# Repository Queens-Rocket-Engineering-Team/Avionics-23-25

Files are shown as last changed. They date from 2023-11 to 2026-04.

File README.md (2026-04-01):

# Legacy Repo!!
All QRET avionics hardware and firmware has migrated to:
- https://github.com/Queens-Rocket-Engineering-Team/av-recovery
- https://github.com/Queens-Rocket-Engineering-Team/av-instrumentation
- https://github.com/Queens-Rocket-Engineering-Team/av-telemetry
- http://github.com/Queens-Rocket-Engineering-Team/av-prop
- https://github.com/Queens-Rocket-Engineering-Team/av-power
- https://github.com/Queens-Rocket-Engineering-Team/av-libraries

# QRET Avionics (2023-2026)

This repository is the working space for QRET's 2023-2026 Avionics systems. This includes both hardware design and firmware projects.

If you're contributing, **make sure you're working in a branch other than Main.**

## Branch Naming Conventions
If you create a new branch, make sure its name includes:
- The subject you're working on
- Hardware (HW) or Firmware (FW)

Examples: `Altimeter_HW`, `Sensors_FW`

Currently we're using KiCAD 8.0.6.

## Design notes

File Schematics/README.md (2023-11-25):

# Schematics

This directory contains all schematics involved in this iteration of the Avionics system.

## Backplane
- Single, large PCB
- Connects all stack "modules" (PCBs)
- Allows communication between modules
- Cleaner routing for power

## GPS Module
- Acquires GPS signal
- Logs GPS data locally

## Communications Module
- Tracks data from other modules using CANBUS
- Remotely transmits data to ground station

## Altimter Module
- Tracks altitude using pressure and accelerometer
- Deploys parachute charges
- Logs altitude, pressure, events, etc. locally

## Sensors Module
- Has various on-board sensors
- Logs data from above sensors locally

## Power Module
- Facilitates connections between backplane and external devices
	- Batteries
	- Screw switches

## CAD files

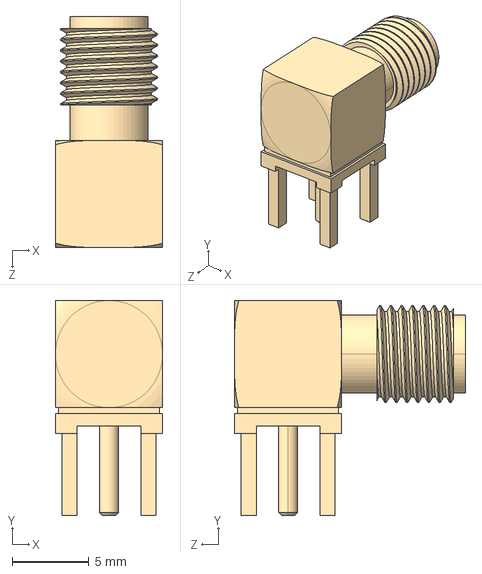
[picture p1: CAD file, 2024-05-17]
Schematics/Communications_Module/models/RF2-03E-T-00-50-G_SMA.STEP
7.00 x 14.1 x 15.1 mm

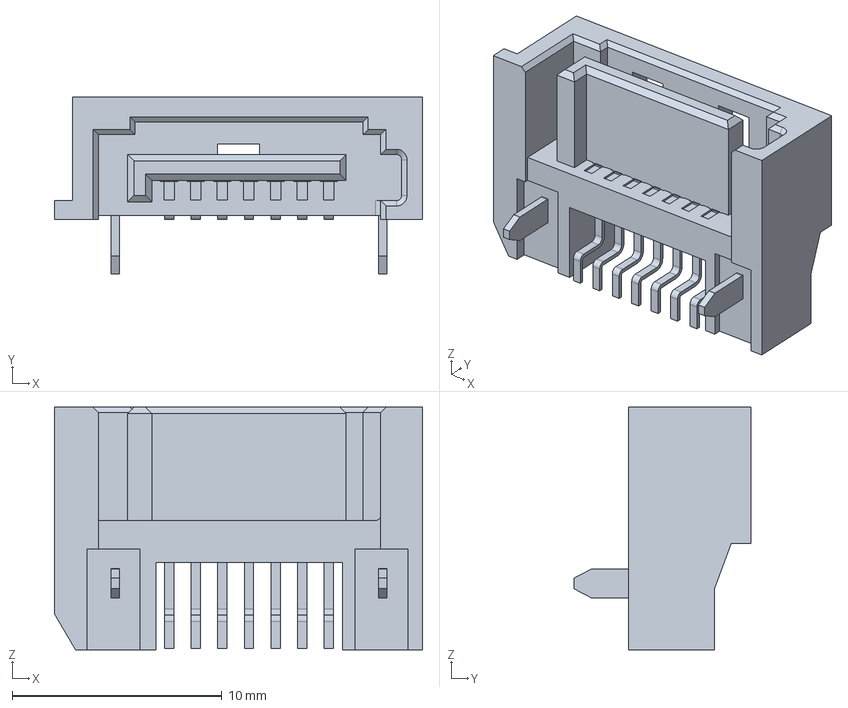
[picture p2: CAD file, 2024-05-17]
Schematics/GPS_Antenna_Board/models/CONN_47080-4001_MOL_SATA.stp
17.5 x 8.45 x 11.6 mm

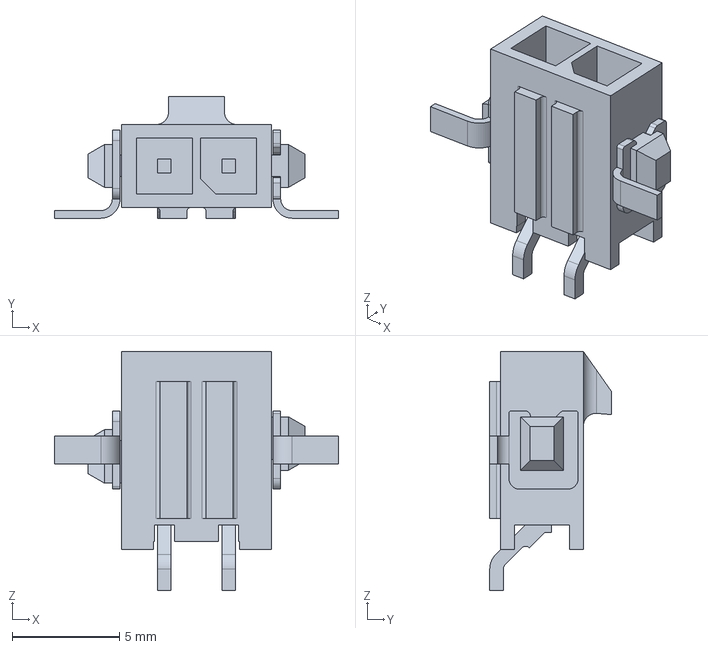
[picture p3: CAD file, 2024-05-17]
Schematics/Power_Module/models/c-2-1445057-2-d-3d.stp
13.2 x 5.67 x 11.2 mm

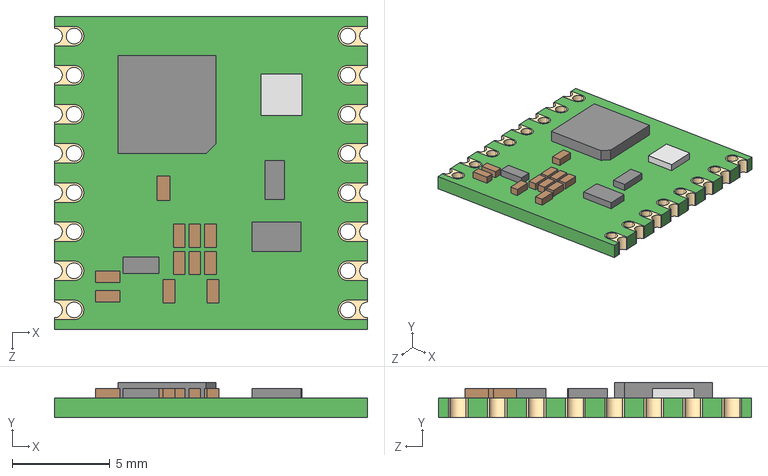
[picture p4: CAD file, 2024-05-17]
Schematics/Communications_Module/models/RFM95W-915S2.step
16.0 x 1.80 x 16.0 mm

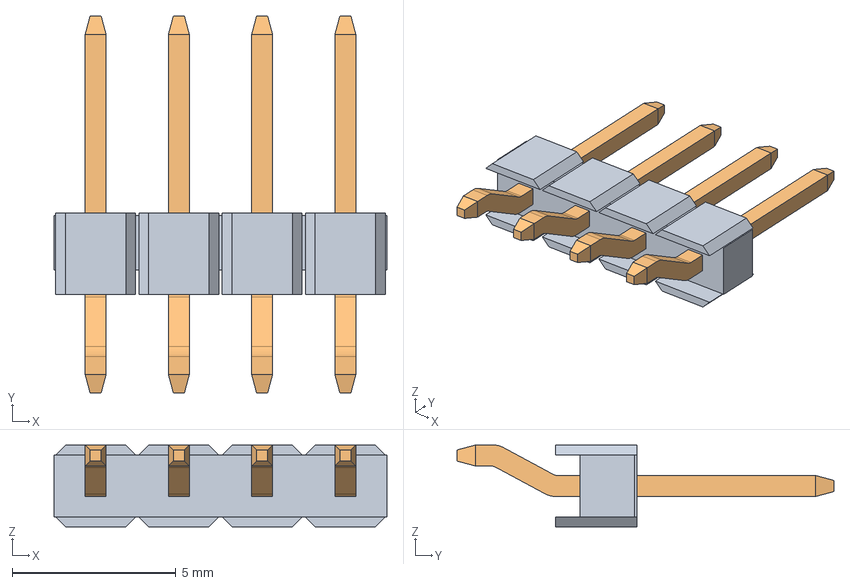
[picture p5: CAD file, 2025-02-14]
Schematics/Altimeter_Module/models/8890445_SWD_PINS.stp
10.2 x 11.5 x 2.50 mm

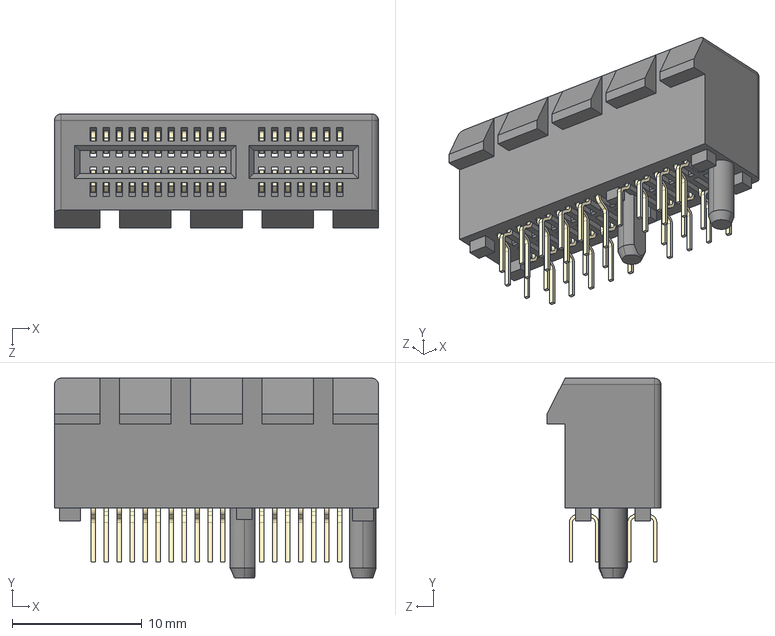
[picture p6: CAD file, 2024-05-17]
Schematics/Backplane/models/10018784-10210TLF.step
25.0 x 15.4 x 8.80 mm

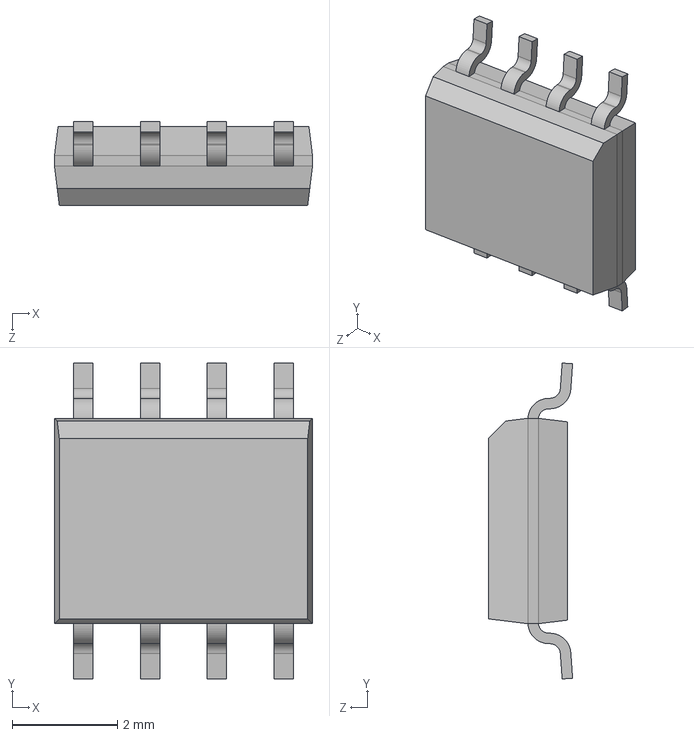
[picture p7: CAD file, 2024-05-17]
Schematics/Altimeter_Module/models/ACS70331EOLCTR-2P5U3.stp
4.90 x 6.00 x 1.60 mm

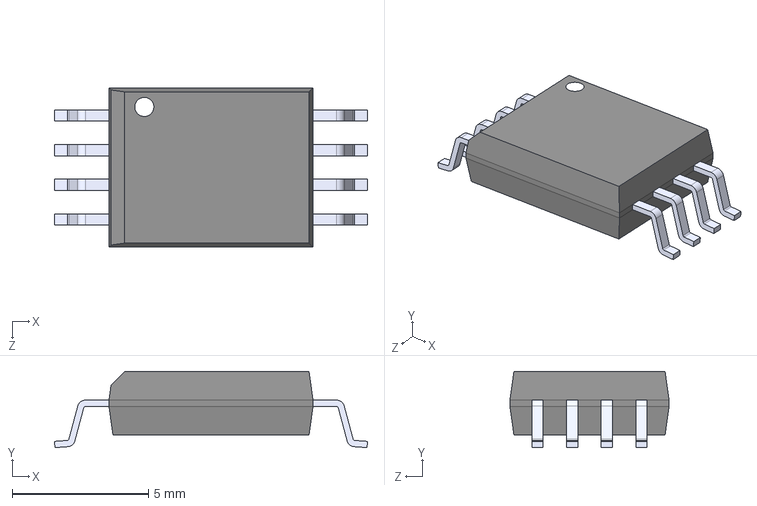
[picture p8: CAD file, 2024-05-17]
Schematics/GPS_Module/models/ISO1042BDWVR.step
11.5 x 2.80 x 5.85 mm

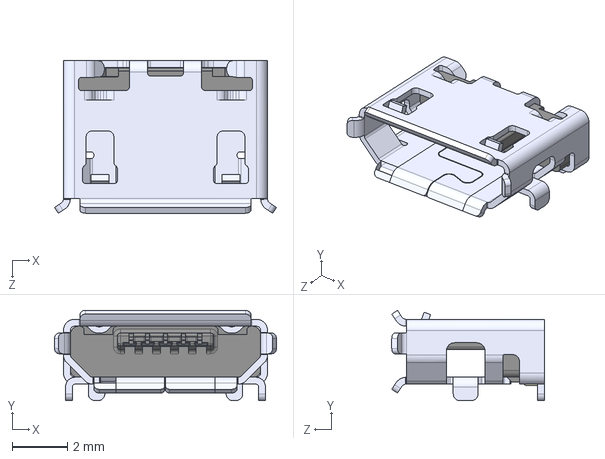
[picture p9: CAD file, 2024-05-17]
Schematics/GPS_Module/models/10118194-0001LF-USB.step
8.05 x 3.27 x 5.53 mm

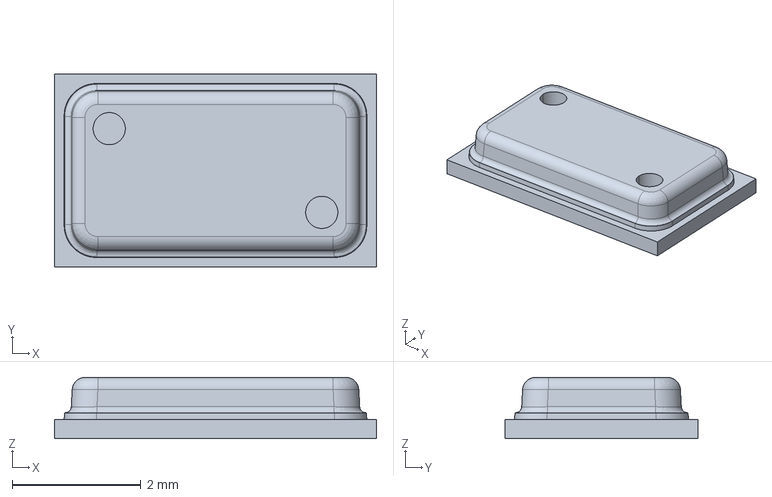
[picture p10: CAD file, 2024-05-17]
Schematics/Altimeter_Module/models/MS560702BA03-50.step
5.00 x 3.00 x 0.95 mm

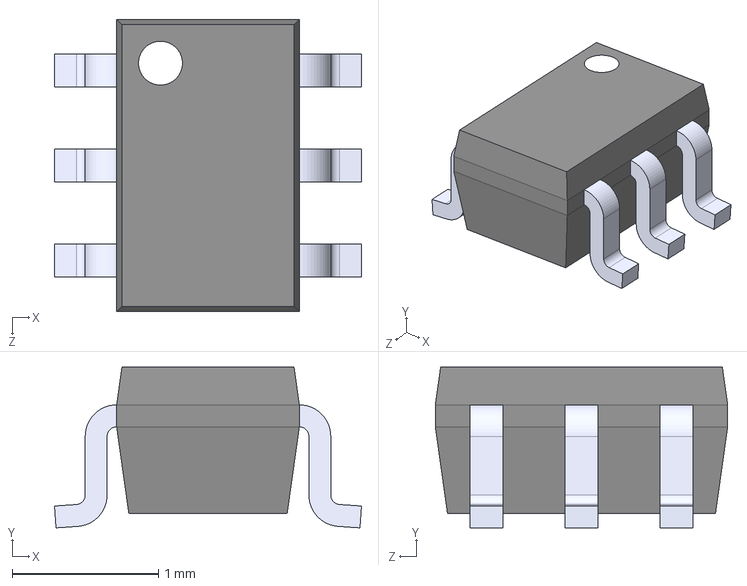
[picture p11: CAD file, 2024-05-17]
Schematics/GPS_Module/models/LM66100DCKR.step
2.10 x 1.10 x 2.00 mm

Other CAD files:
Schematics/Altimeter_Module/models/CONN_2-1445057-2_AMP.step

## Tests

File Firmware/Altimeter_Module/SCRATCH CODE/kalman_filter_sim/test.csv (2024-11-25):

Time | Actual Altitude | Measured Altitude | Estimated Altitude | Actual Velocity | Estimated Velocity
0 | 0.0045 | -0.1955 | -0.101693 | 0.3 | 0.195812
0.01 | 0.012 | 0.212 | 0.0209463 | 0.6 | 0.614993
0.02 | 0.0225 | -0.1775 | -0.0386365 | 0.9 | 0.84776
0.03 | 0.036 | 0.136 | 0.0205453 | 1.2 | 1.19597
0.04 | 0.0525 | 0.4525 | 0.153328 | 1.5 | 1.61529
0.05 | 0.072 | -0.228 | 0.0600471 | 1.8 | 1.80436
0.06 | 0.0945 | -0.4055 | -0.0534859 | 2.1 | 1.97128
0.07 | 0.12 | -0.08 | -0.0452763 | 2.4 | 2.25728
0.08 | 0.1485 | -0.3515 | -0.110828 | 2.7 | 2.46666
0.09 | 0.18 | -0.12 | -0.0942345 | 3 | 2.7561
0.1 | 0.2145 | -0.1855 | -0.0977243 | 3.3 | 3.02255
0.11 | 0.252 | 0.452 | 0.074034 | 3.6 | 3.46258
0.12 | 0.2925 | -0.00750001 | 0.0783585 | 3.9 | 3.72979
0.13 | 0.336 | 0.036 | 0.0952273 | 4.2 | 4.00786
0.14 | 0.3825 | 0.5825 | 0.257225 | 4.5 | 4.42828
0.15 | 0.432 | 0.832 | 0.445922 | 4.8 | 4.8702
0.16 | 0.4845 | 0.1845 | 0.411931 | 5.1 | 5.08501
0.17 | 0.54 | 0.94 | 0.592801 | 5.4 | 5.51353
0.18 | 0.5985 | 0.3985 | 0.58164 | 5.7 | 5.74474
0.19 | 0.66 | 0.26 | 0.537766 | 6 | 5.94092
0.2 | 0.7245 | 1.1245 | 0.74073 | 6.3 | 6.38298
0.21 | 0.792 | 0.392 | 0.694199 | 6.6 | 6.57112
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

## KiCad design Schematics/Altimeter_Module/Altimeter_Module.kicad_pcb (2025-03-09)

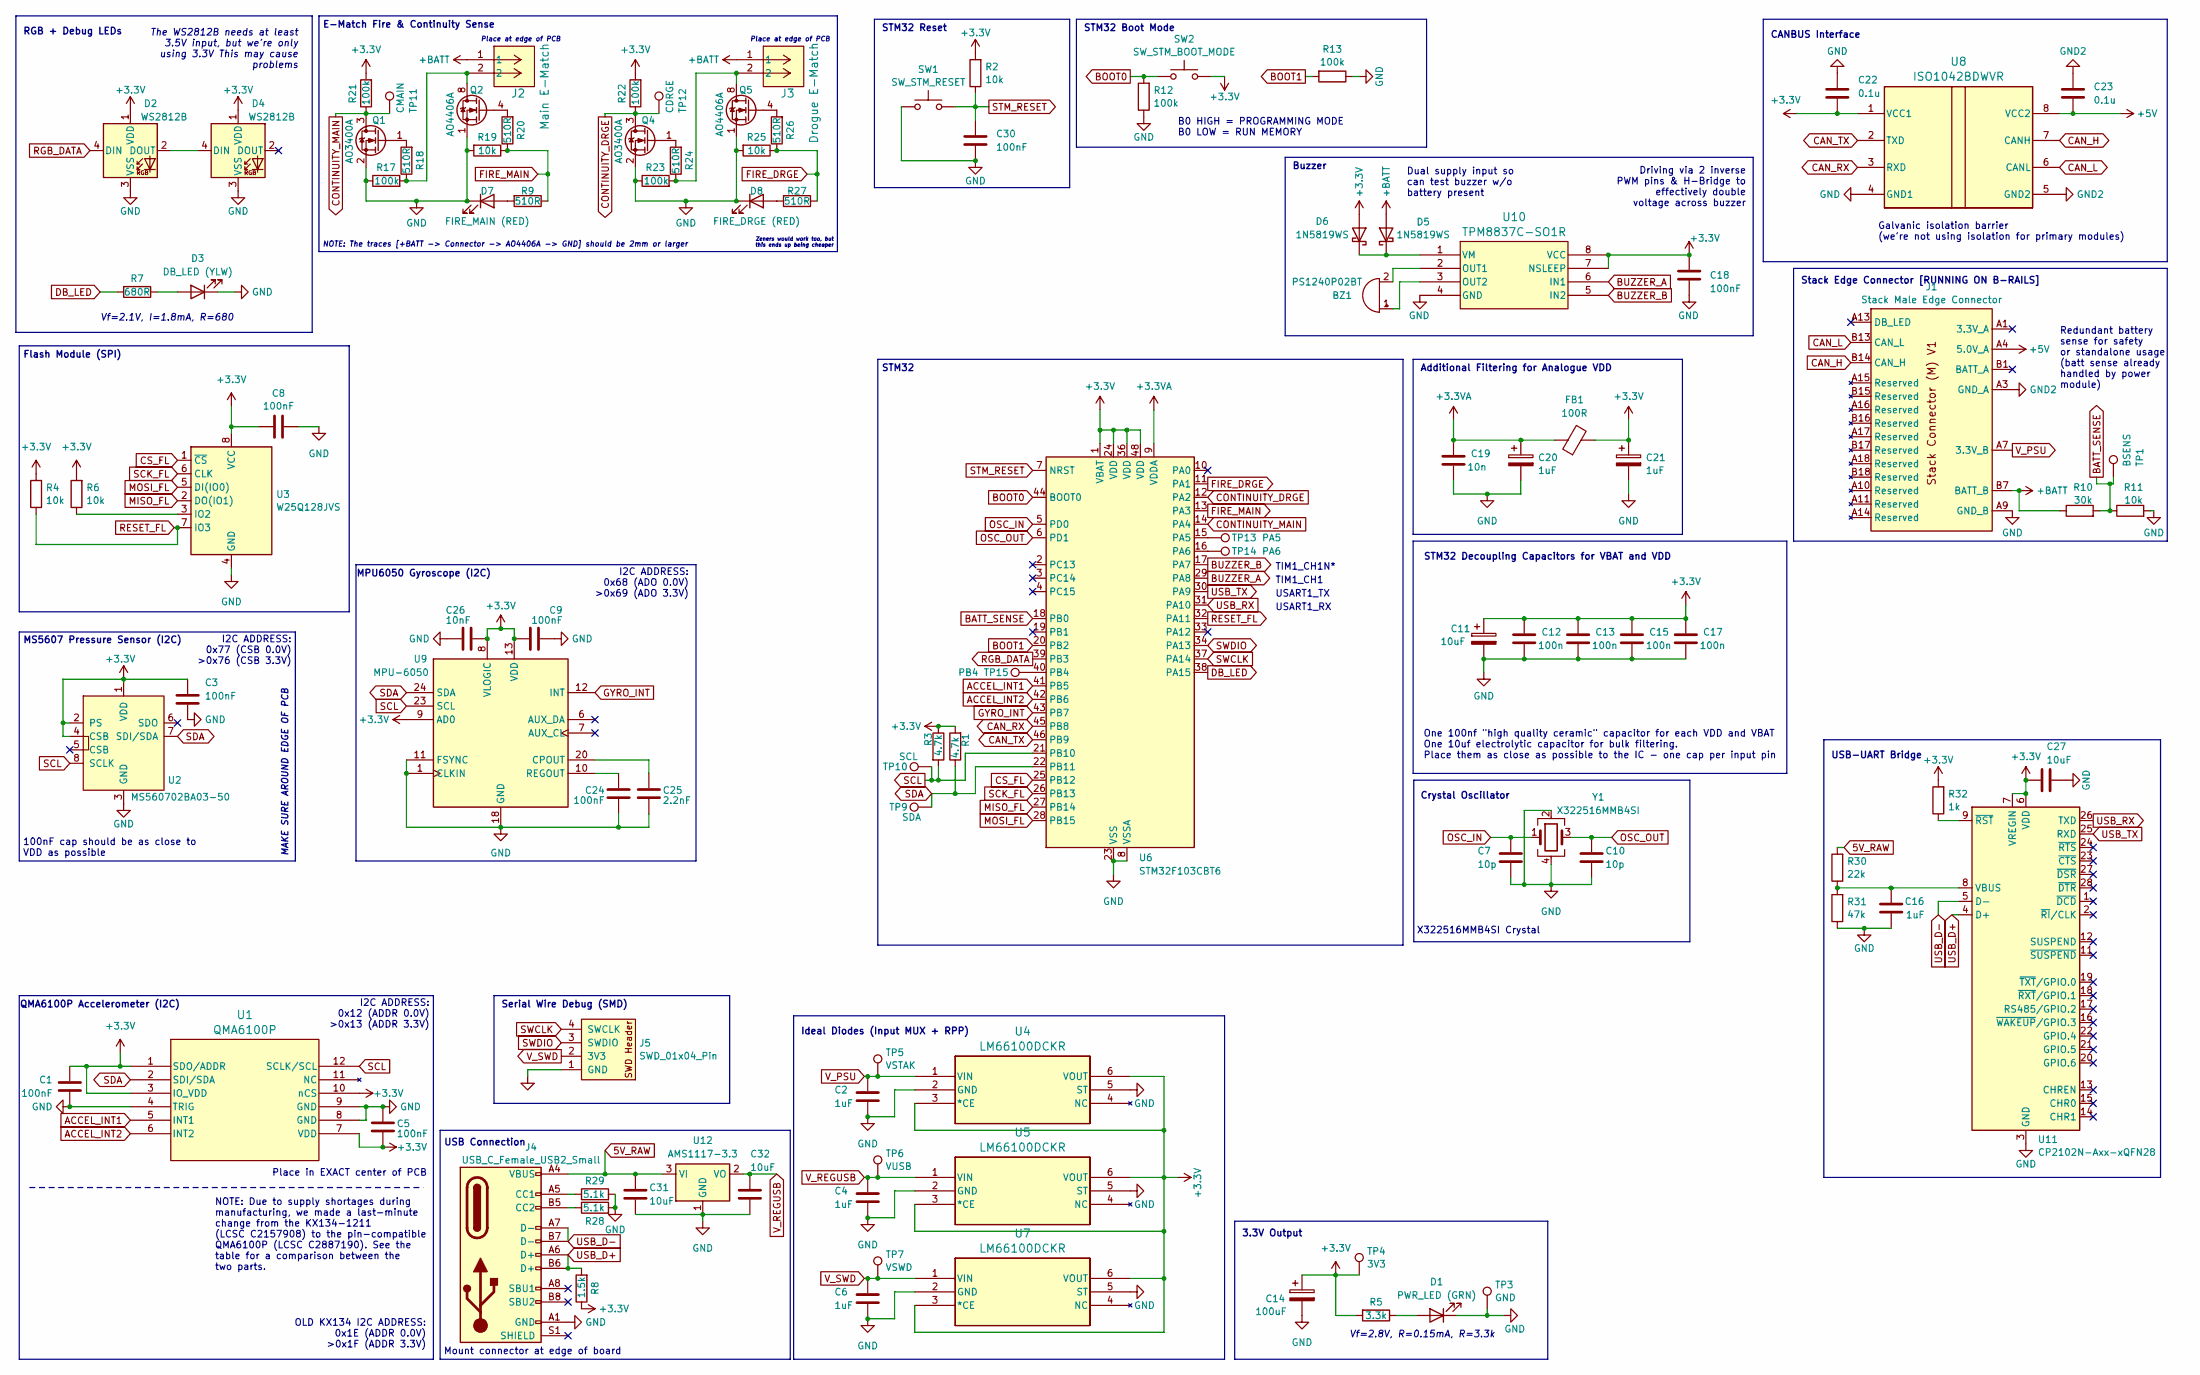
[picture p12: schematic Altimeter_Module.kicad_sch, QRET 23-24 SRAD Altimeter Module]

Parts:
BZ1: PS1240P02BT; Buzzer_12.6x9.5RM5.0; Digikey 445-2525-1-ND
C1, C3, C5, C8, C9, C18, C24, C30: 100nF; C_0603_1608Metric; JLCPCB C14663
C2, C4, C6, C16: 1uF; C_0603_1608Metric; JLCPCB C15849
C7, C10: 10p; C_0603_1608Metric; JLCPCB C1634
C11: 10uF; CP_Elec_4x5.4; Digikey 732-8411-1-ND
C12, C13, C15, C17: 100n; C_0402_1005Metric; JLCPCB C1525
C14: 100uF; CP_Elec_6.3x5.9; Digikey 732-8419-1-ND
C19: 10n; C_0603_1608Metric; JLCPCB C57112
C20, C21: 1uF; C_0805_2012Metric; JLCPCB C28323
C22, C23: 0.1u; C_0603_1608Metric; JLCPCB C14663
C25: 2.2nF; C_0603_1608Metric; JLCPCB C1604
C26: 10nF; C_0603_1608Metric; JLCPCB C57112
C27, C31, C32: 10uF; C_0603_1608Metric; JLCPCB C96446
D1: PWR_LED (GRN); LED_0805_2012Metric; JLCPCB C2297
D2, D4: WS2812B; LED_WS2812B_PLCC4_5.0x5.0mm_P3.2mm; Digikey 1568-COM-16347CT-ND
D3: DB_LED (YLW); LED_0603_1608Metric; JLCPCB C72038
D5, D6: 1N5819WS; D_SOD-323; JLCPCB C191023
D7: FIRE_MAIN (RED); LED_0603_1608Metric; JLCPCB C2286
D8: FIRE_DRGE (RED); LED_0603_1608Metric; JLCPCB C2286
FB1: 100R; R_0805_2012Metric; JLCPCB C1015
J1: Stack Male Edge Connector; BUS_PCIexpress_x1
J2: Main E-Match; CONN_2-1445057-2_TYCO; Digikey A33212CT-ND
J3: Drogue E-Match; CONN_2-1445057-2_TYCO; Digikey A33212CT-ND
J4: USB_C_Female_USB2_Small; USB_C_DB-108PWB; JLCPCB C5178541
J5: SWD_01x04_Pin; SWD_PinHeader_1x04_P2.54mm_Horizontal_SMD; Digikey 952-3233-ND
Q1, Q4: AO3400A; SOT-23; JLCPCB C20917
Q2, Q5: AO4406A; SOIC-8_3.9x4.9mm_P1.27mm; JLCPCB C5155213
R1, R3: 4.7k; R_0603_1608Metric; JLCPCB C23162
R2, R4, R6, R11, R19, R25: 10k; R_0603_1608Metric; JLCPCB C25804
R5: 3.3k; R_0603_1608Metric; JLCPCB C22978
R7: 680R; R_0603_1608Metric; JLCPCB C23228
R8: 1.5k; R_0603_1608Metric; JLCPCB C22843
R9, R18, R20, R24, R26, R27: 510R; R_0603_1608Metric; JLCPCB C23193
R10: 30k; R_0603_1608Metric; JLCPCB C22984
R12, R13, R17, R21, R22, R23: 100k; R_0603_1608Metric; JLCPCB C25803
R28, R29: 5.1k; R_0603_1608Metric; JLCPCB C23186
R30: 22k; R_0603_1608Metric; JLCPCB C31850
R31: 47k; R_0603_1608Metric; JLCPCB C25819
R32: 1k; R_0603_1608Metric; JLCPCB C21190
SW1: SW_STM_RESET; SW_Push_1P1T_XKB_TS-1187A; JLCPCB C318884
SW2: SW_STM_BOOT_MODE; SW_Push_1P1T_XKB_TS-1187A; JLCPCB C318884
TP1: BSENS; TestPoint_Pad_1.5x1.5mm
TP3: GND; TestPoint_Pad_1.5x1.5mm
TP4: 3V3; TestPoint_Pad_1.5x1.5mm
TP5: VSTAK; TestPoint_Pad_1.5x1.5mm
TP6: VUSB; TestPoint_Pad_1.5x1.5mm
TP7: VSWD; TestPoint_Pad_1.5x1.5mm
TP9: SDA; TestPoint_Pad_1.5x1.5mm
TP10: SCL; TestPoint_Pad_1.5x1.5mm
TP11: CMAIN; TestPoint_Pad_1.5x1.5mm
TP12: CDRGE; TestPoint_Pad_1.5x1.5mm
TP13: PA5; TestPoint_Pad_1.5x1.5mm
TP14: PA6; TestPoint_Pad_1.5x1.5mm
TP15: PB4; TestPoint_Pad_1.5x1.5mm
U1: QMA6100P; LGA-12_2x2mm_P0.5mm; JLCPCB C2887190
U2: MS560702BA03-50; MS5607_Handsolder; Digikey 223-1198-1-ND
U3: W25Q128JVS; SOIC-8_5.23x5.23mm_P1.27mm; JLCPCB C97521
U4, U5, U7: LM66100DCKR; SC-70-6_Handsoldering; JLCPCB C2869734
U6: STM32F103CBT6; LQFP-48_7x7mm_P0.5mm; JLCPCB C8304
U8: ISO1042BDWVR; SOIC-8 ISO1042BDWV; JLCPCB C484409
U9: MPU-6050; InvenSense_QFN-24_4x4mm_P0.5mm; JLCPCB C24112
U10: TPM8837C-SO1R; SOP-8_TPK; Digikey 5503-TPM8837C-SO1RCT-ND
U11: CP2102N-Axx-xQFN28; QFN-28-1EP_5x5mm_P0.5mm_EP3.35x3.35mm; JLCPCB C6568
U12: AMS1117-3.3; SOT-223-3_TabPin2; JLCPCB C6186
Y1: X322516MMB4SI; Crystal_SMD_3225-4Pin_3.2x2.5mm; JLCPCB C13738

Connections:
5V_RAW: C31.1, J4.A4 (VBUS), J4.A9 (VBUS), J4.B4 (VBUS), J4.B9 (VBUS), R30.2, U12.3 (VI)
+3.3V: C1.1, C3.1, C5.2, C8.1, C9.1, C11.1, C12.1, C13.1, C14.1, C15.1, C17.1, C18.1, C21.1, C22.2, C26.1, C27.2, D2.1 (VDD), D4.1 (VDD), D6.2 (A), FB1.2, R1.2, R2.2, R3.1, R4.2, R5.2, R6.2, R8.1, R21.2, R22.2, R32.2, SW2.2, TP4.1, U1.1 (SDO/ADDR), U1.3 (IO_VDD), U1.7 (VDD), U1.10 (nCS), U2.1 (VDD), U2.2 (PS), U2.4 (CSB), U3.8 (VCC), U4.3 (*CE), U4.6 (VOUT), U5.3 (*CE), U5.6 (VOUT), U6.1 (VBAT), U6.24 (VDD), U6.36 (VDD), U6.48 (VDD), U7.3 (*CE), U7.6 (VOUT), U8.1 (VCC1), U9.8 (VLOGIC), U9.9 (AD0), U9.13 (VDD), U10.7 (NSLEEP), U10.8 (VCC), U11.6 (VDD), U11.7 (VREGIN)
+3.3VA: C19.1, C20.1, FB1.1, U6.9 (VDDA)
+5V: C23.2, J1.A4 (5.0V_A), J1.A5 (5.0V_A), U8.8 (VCC2)
+BATT: D5.2 (A), J1.B7 (BATT_B), J1.B8 (BATT_B), J1.B9 (BATT_B), J2.1, J3.1, R10.1
ACCEL_INT1: U1.5 (INT1), U6.41 (PB5)
ACCEL_INT2: U1.6 (INT2), U6.42 (PB6)
BATT_SENSE: R10.2, R11.1, TP1.1, U6.18 (PB0)
BOOT0: R12.2, SW2.1, U6.44 (BOOT0)
BOOT1: R13.2, U6.20 (PB2)
BUZZER_A: U6.29 (PA8), U10.6 (IN1)
BUZZER_B: U6.17 (PA7), U10.5 (IN2)
CAN_H: J1.B14 (CAN_H), U8.7 (CANH)
CAN_L: J1.B13 (CAN_L), U8.6 (CANL)
CAN_RX: U6.45 (PB8), U8.3 (RXD)
CAN_TX: U6.46 (PB9), U8.2 (TXD)
CONTINUITY_DRGE: Q4.3 (D), R22.1, TP12.1, U6.12 (PA2)
CONTINUITY_MAIN: Q1.3 (D), R21.1, TP11.1, U6.14 (PA4)
CS_FL: U3.1 (~CS), U6.25 (PB12)
DB_LED: R7.2, U6.38 (PA15)
FIRE_DRGE: R25.1, R26.1, R27.1, U6.11 (PA1)
FIRE_MAIN: R9.1, R19.1, R20.1, U6.13 (PA3)
GND: C1.2, C2.2, C3.2, C4.2, C5.1, C6.2, C7.2, C8.2, C9.2, C10.2, C11.2, C12.2, C13.2, C14.2, C15.2, C16.1, C17.2, C18.2, C19.2, C20.2, C21.2, C22.1, C24.2, C25.2, C26.2, C27.1, C30.2, C31.2, C32.2, D1.1 (K), D2.3 (VSS), D3.1 (K), D4.3 (VSS), D7.1 (K), D8.1 (K), J1.A9 (GND_B), J1.A12 (GND_B), J1.B10 (GND_B), J1.B11 (GND_B), J1.B12 (GND_B), J4.A1 (GND), J4.A12 (GND), J4.B1 (GND), J4.B12 (GND), J5.1 (GND), Q1.2 (S), Q2.1 (S), Q2.2 (S), Q2.3 (S), Q4.2 (S), Q5.1 (S), Q5.2 (S), Q5.3 (S), R11.2, R12.1, R13.1, R17.1, R19.2, R23.1, R25.2, R28.2, R29.2, R31.1, SW1.1, TP3.1, U1.4 (TRIG), U1.8 (GND), U1.9 (GND), U2.3 (GND), U3.4 (GND), U4.2 (GND), U4.5 (ST), U5.2 (GND), U5.5 (ST), U6.8 (VSSA), U6.23 (VSS), U6.35 (VSS), U6.47 (VSS), U7.2 (GND), U7.5 (ST), U8.4 (GND1), U9.1 (CLKIN), U9.11 (FSYNC), U9.18 (GND), U10.4 (GND), U11.3 (GND), U11.29 (GND), U12.1 (GND), Y1.2, Y1.4
GND2: C23.1, J1.A3 (GND_A), J1.A6 (GND_A), J1.B4 (GND_A), J1.B5 (GND_A), J1.B6 (GND_A), U8.5 (GND2)
GYRO_INT: U6.43 (PB7), U9.12 (INT)
MISO_FL: U3.2 (DO(IO1)), U6.27 (PB14)
MOSI_FL: U3.5 (DI(IO0)), U6.28 (PB15)
unnamed: BZ1.2 (+), U10.2 (OUT1)
unnamed: BZ1.1 (-), U10.3 (OUT2)
unnamed: D1.2 (A), R5.1
unnamed: D2.2 (DOUT), D4.4 (DIN)
unnamed: D3.2 (A), R7.1
unnamed: D5.1 (K), D6.1 (K), U10.1 (VM)
unnamed: D7.2 (A), R9.2
unnamed: D8.2 (A), R27.2
unnamed: J2.2, Q2.5 (D), Q2.6 (D), Q2.7 (D), Q2.8 (D), R17.2, R18.1
unnamed: J3.2, Q5.5 (D), Q5.6 (D), Q5.7 (D), Q5.8 (D), R23.2, R24.1
unnamed: J4.A5 (CC1), R29.1
unnamed: J4.B5 (CC2), R28.1
unnamed: Q1.1 (G), R18.2
unnamed: Q2.4 (G), R20.2
unnamed: Q4.1 (G), R24.2
unnamed: Q5.4 (G), R26.2
unnamed: R6.1, U3.3 (IO2)
unnamed: TP13.1, U6.15 (PA5)
unnamed: TP14.1, U6.16 (PA6)
unnamed: TP15.1, U6.40 (PB4)
unnamed: C25.1, U9.20 (CPOUT)
unnamed: C24.1, U9.10 (REGOUT)
unnamed: C16.2, R30.1, R31.2, U11.8 (VBUS)
unnamed: R32.1, U11.9 (~RST)
OSC_IN: C7.1, U6.5 (PD0), Y1.1
OSC_OUT: C10.1, U6.6 (PD1), Y1.3
RESET_FL: R4.1, U3.7 (IO3), U6.32 (PA11)
RGB_DATA: D2.4 (DIN), U6.39 (PB3)
SCK_FL: U3.6 (CLK), U6.26 (PB13)
SCL: R3.2, TP10.1, U1.12 (SCLK/SCL), U2.8 (SCLK), U6.21 (PB10), U9.23 (SCL)
SDA: R1.1, TP9.1, U1.2 (SDI/SDA), U2.7 (SDI/SDA), U6.22 (PB11), U9.24 (SDA)
STM_RESET: C30.1, R2.1, SW1.2, U6.7 (NRST)
SWCLK: J5.4 (SWCLK), U6.37 (PA14)
SWDIO: J5.3 (SWDIO), U6.34 (PA13)
USB_D+: J4.A6 (D+), J4.B6 (D+), R8.2, U11.4 (D+)
USB_D-: J4.A7 (D-), J4.B7 (D-), U11.5 (D-)
USB_RX: U6.31 (PA10), U11.26 (TXD)
USB_TX: U6.30 (PA9), U11.25 (RXD)
V_PSU: C2.1, J1.A7 (3.3V_B), J1.A8 (3.3V_B), TP5.1, U4.1 (VIN)
V_REGUSB: C4.1, C32.1, TP6.1, U5.1 (VIN), U12.2 (VO)
V_SWD: C6.1, J5.2 (3V3), TP7.1, U7.1 (VIN)

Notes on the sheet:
Serial Wire Debug (SMD)
Flash Module (SPI)
RGB + Debug LEDs
The WS2812B needs at least 3.5V input, but we're only using 3.3V This may cause problems
Additional Filtering for Analogue VDD
Stack Edge Connector [RUNNING ON B-RAILS]
NOTE: Due to supply shortages during manufacturing, we made a last-minute change from the KX134-1211 (LCSC C2157908) to the pin-compatible QMA6100P (LCSC C2887190). See the table for a comparison between the two parts.
Buzzer
Place at edge of PCB
Ideal Diodes (Input MUX + RPP)
Crystal Oscillator
Vf=2.1V, I=1.8mA, R=680
STM32
I2C ADDRESS: 0x12 (ADDR 0.0V) >0x13 (ADDR 3.3V)
B0 HIGH = PROGRAMMING MODE B0 LOW = RUN MEMORY
USART1_TX
USART1_RX
MS5607 Pressure Sensor (I2C)
Place in EXACT center of PCB
3.3V Output
OLD KX134 I2C ADDRESS: 0x1E (ADDR 0.0V) >0x1F (ADDR 3.3V)
Mount connector at edge of board
X322516MMB4SI Crystal
CANBUS Interface
STM32 Decoupling Capacitors for VBAT and VDD
I2C ADDRESS: 0x68 (ADO 0.0V) >0x69 (ADO 3.3V)
STM32 Boot Mode
TIM1_CH1N*
TIM1_CH1
QMA6100P Accelerometer (I2C)
E-Match Fire & Continuity Sense
Galvanic isolation barrier (we're not using isolation for primary modules)
One 100nf "high quality ceramic" capacitor for each VDD and VBAT One 10uf electrolytic capacitor for bulk filtering. Place them as close as possible to the IC - one cap per input pin
NOTE: The traces [+BATT -> Connector -> AO4406A -> GND] should be 2mm or larger
Zeners would work too, but this ends up being cheaper
MAKE SURE AROUND EDGE OF PCB
Driving via 2 inverse PWM pins & H-Bridge to effectively double voltage across buzzer
100nF cap should be as close to VDD as possible
I2C ADDRESS: 0x77 (CSB 0.0V) >0x76 (CSB 3.3V)
STM32 Reset

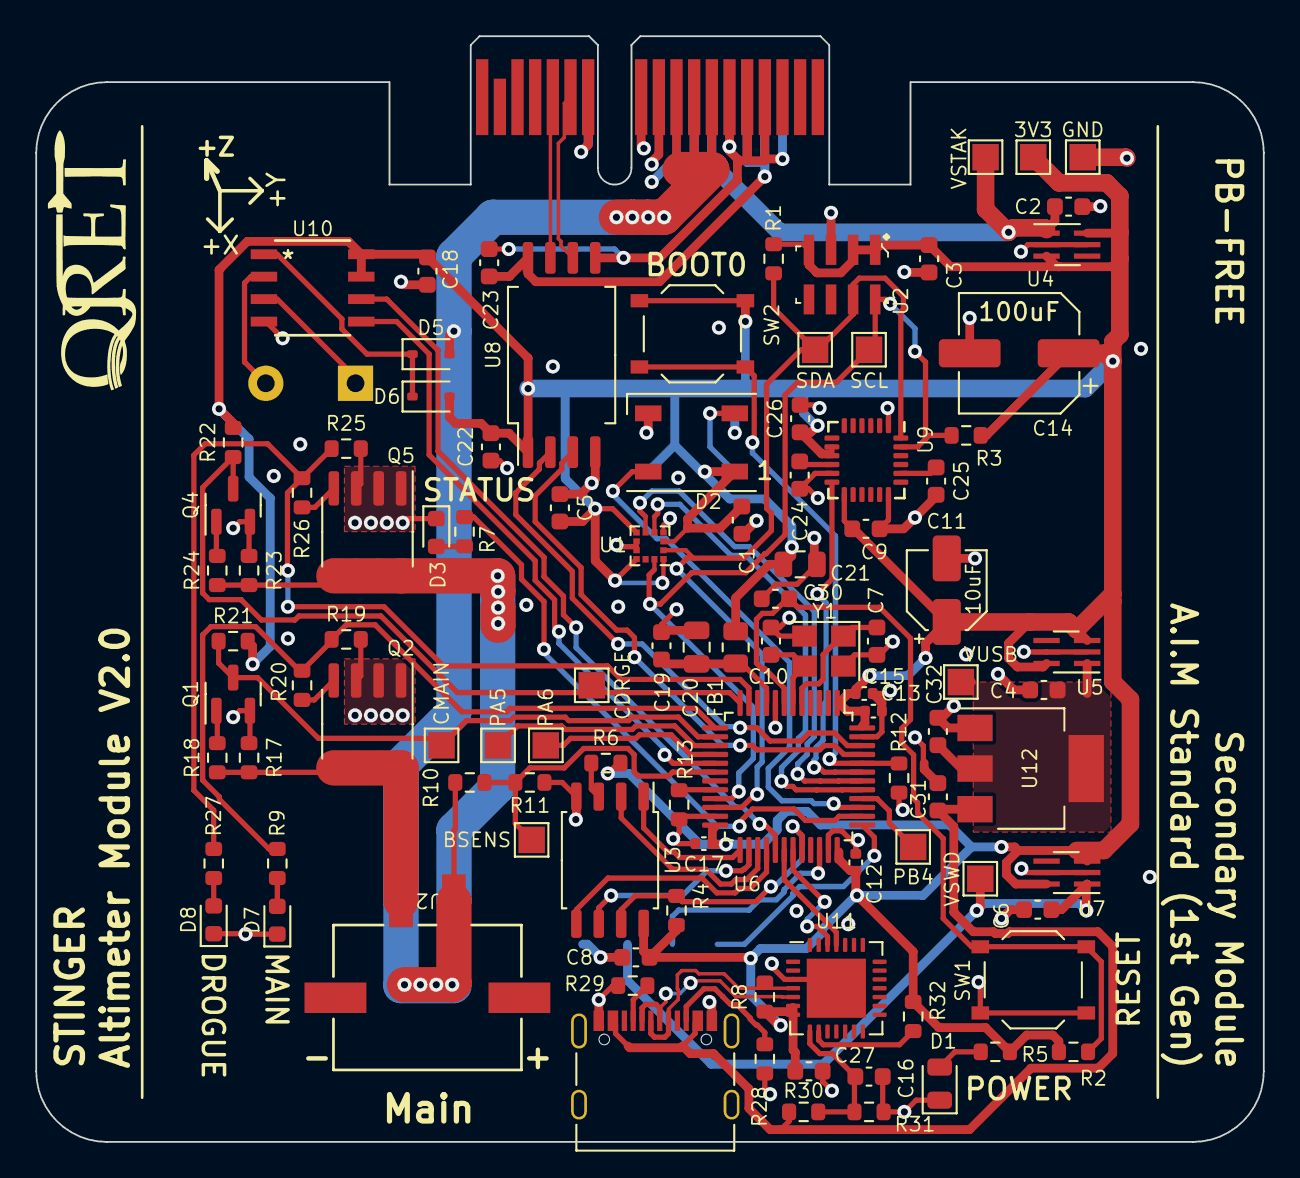
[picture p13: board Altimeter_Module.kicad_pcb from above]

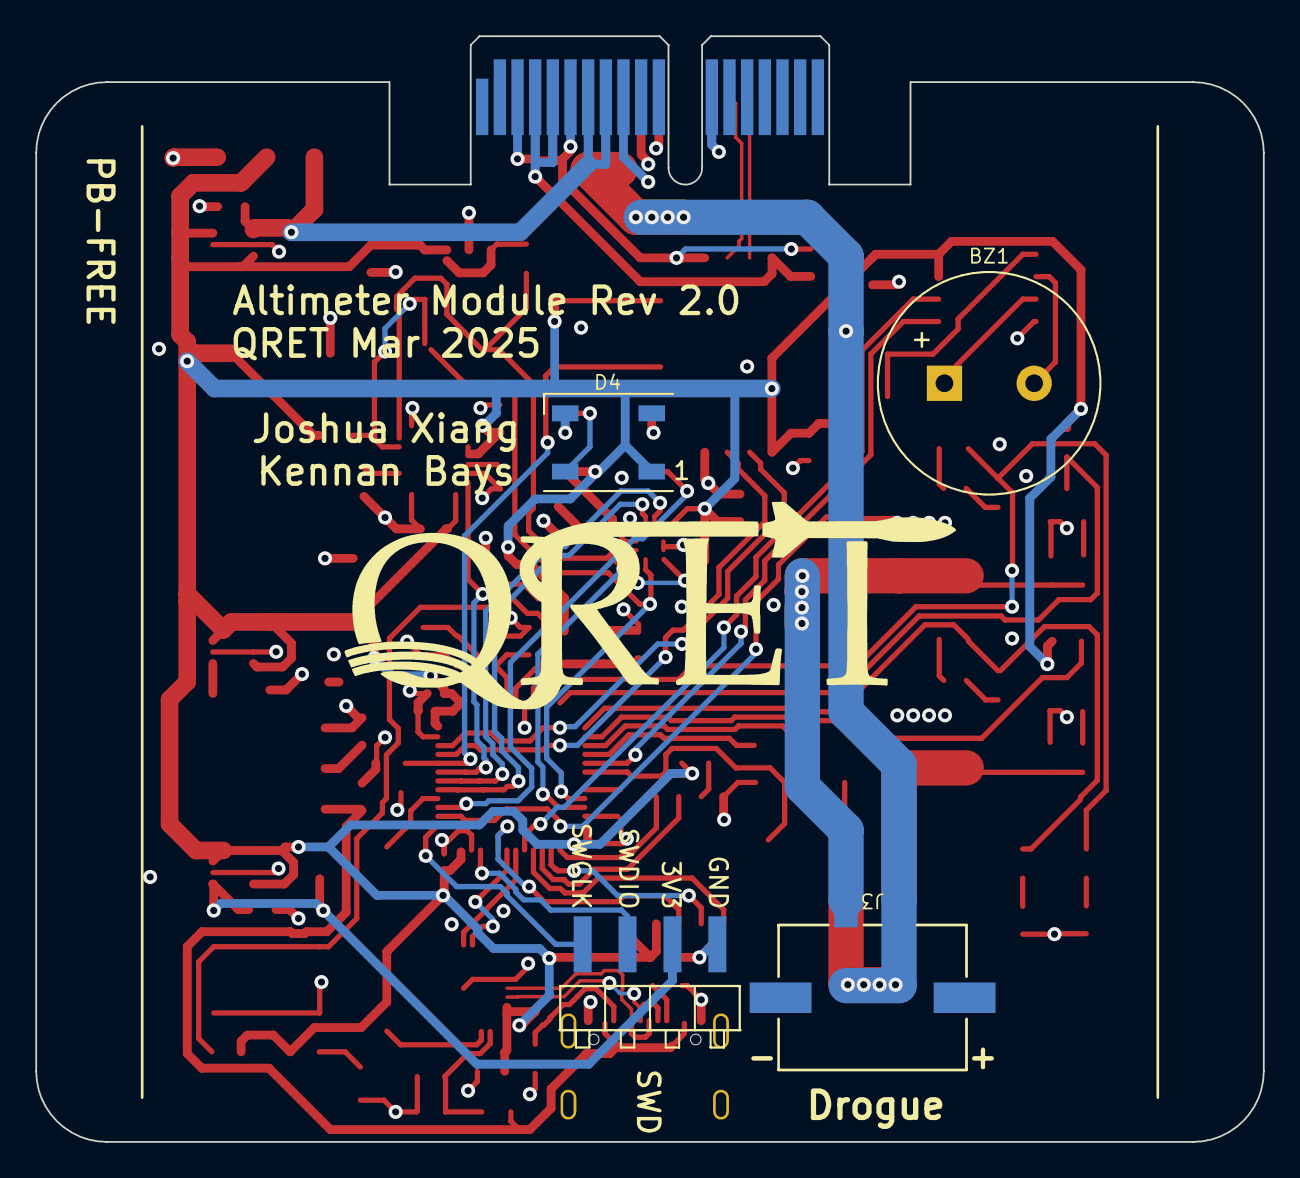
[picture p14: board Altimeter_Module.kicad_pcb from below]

Board: 4 copper layers, 69.5 x 62.6 mm, 106 parts (4 on the bottom side), 68 nets.

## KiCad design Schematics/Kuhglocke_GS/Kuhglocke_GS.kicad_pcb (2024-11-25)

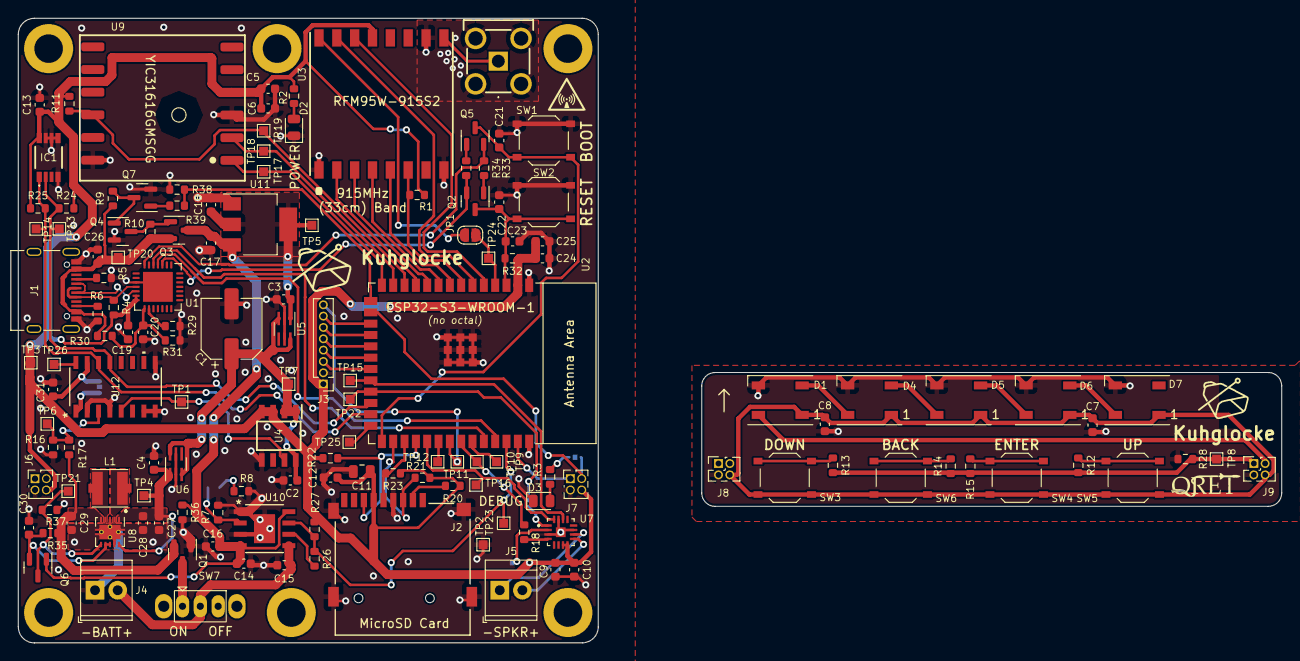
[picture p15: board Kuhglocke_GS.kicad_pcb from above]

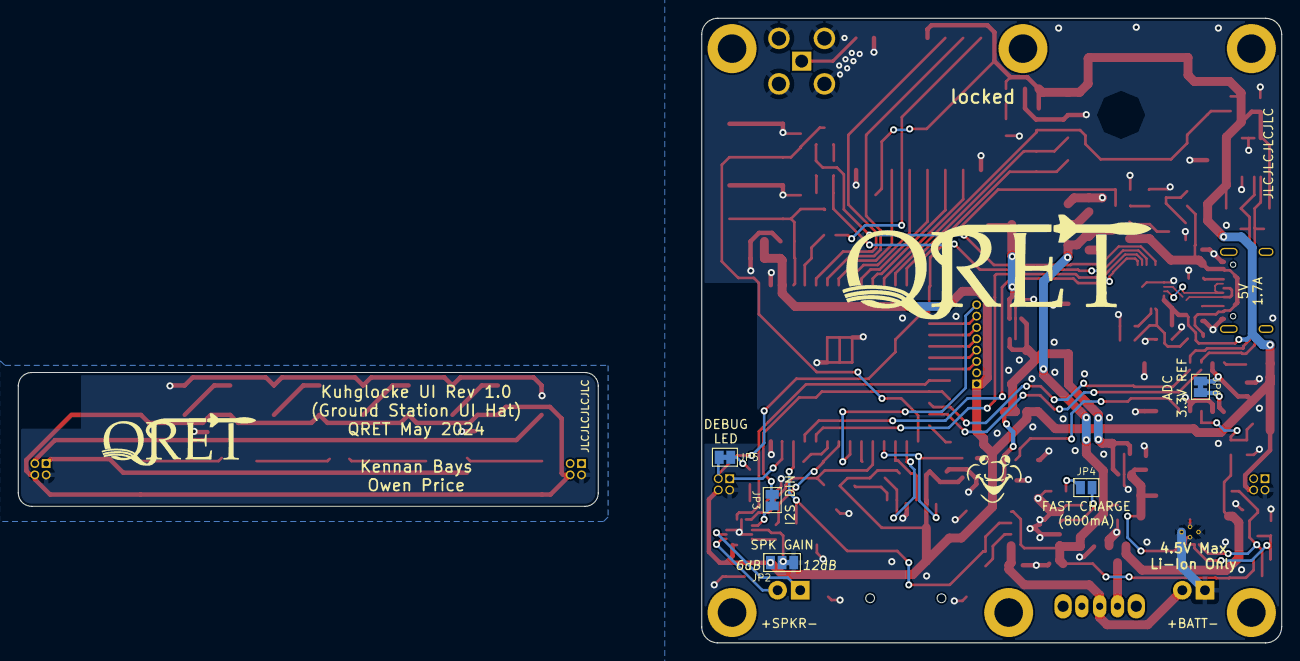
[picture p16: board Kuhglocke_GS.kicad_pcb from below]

Board: 2 copper layers, 65.0 x 70.0 mm, 152 parts (5 on the bottom side), 94 nets.

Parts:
AE1: Antenna; PCB114SMAFRAJA
C1: 100uF; CP_Elec_6.3x5.9
C2, C5, C9, C12, C13, C16, C21, C22, C25, C30: 0.1uF; C_0603_1608Metric
C3, C4, C7, C8, C14, C15, C20, C23, C31: 1uF; C_0603_1608Metric
C6: 4.7uF; C_0603_1608Metric
C10, C17, C18, C19, C24, C26, C27, C28, C29: 10uF; C_0603_1608Metric
C11: 47uF; C_0805_2012Metric
D1, D4, D5, D6, D7: WS2812B; LED_WS2812B_PLCC4_5.0x5.0mm_P3.2mm
D2: INT_PWR_LED (RED); LED_0805_2012Metric
D3: DB_LED (GRN); LED_0805_2012Metric
H1, H2, H3, H4, H5, H6: MountingHole; MountingHole_3.2mm_M3_ISO14580_Pad
IC1: P3T1755DPZ
J1: USB_C_Female_USB2_Small; USB_C_DB-108PWB
J2: MSD-1-A MicroSD Slot; MicroSD_MSD-1-A
J3: PinHeader_1x08_P1.27mm_Vertical
J4: 1S Li-Ion Cell; TerminalBlock_TE_282834-2_1x02_P2.54mm_Horizontal
J5: Speaker; TerminalBlock_TE_282834-2_1x02_P2.54mm_Horizontal
J6: MB_A; PinSocket_2x02_P1.27mm_Vertical
J7: MB_B; PinSocket_2x02_P1.27mm_Vertical
J8: DB_A; HPH2-A-04-UA_PINS
J9: DB_B; HPH2-A-04-UA_PINS
JP1: DIO2_EN; SolderJumper-2_P1.3mm_Open_RoundedPad1.0x1.5mm
JP2: Gain; SolderJumper-3_P1.3mm_Bridged12_Pad1.0x1.5mm_NumberLabels
JP3: SPK_DIN; SolderJumper-2_P1.3mm_Bridged_Pad1.0x1.5mm
JP4: FastCharge; SolderJumper-2_P1.3mm_Open_Pad1.0x1.5mm
JP5: DB_LED_EN; SolderJumper-2_P1.3mm_Bridged_Pad1.0x1.5mm
JP6: ADC_REFP; SolderJumper-2_P1.3mm_Bridged_Pad1.0x1.5mm
L1: 2.2uH; L_Taiyo-Yuden_MD-4040
Q1, Q3, Q6: AO3401A; SOT-23
Q2, Q5: MMBT3904; SOT-23
Q4, Q7: AO3400A; SOT-23
R1, R3, R11, R16, R17, R20, R21, R22, R23, R26, R27, R32, R33, R34: 10k; R_0603_1608Metric
R2: 1.8k; R_0603_1608Metric
R4: 1.5k; R_0603_1608Metric
R5, R6: 5.1k; R_0603_1608Metric
R7: 2.4k; R_0603_1608Metric
R8: 3.9k; R_0603_1608Metric
R9, R18, R36, R38: 100k; R_0603_1608Metric
R10, R37: 51k; R_0603_1608Metric
R12, R39: 510; R_0603_1608Metric
R13, R28, R29: 1k; R_0603_1608Metric
R14: 2k; R_0603_1608Metric
R15: 5.6k; R_0603_1608Metric
R24, R25: 4.7k; R_0603_1608Metric
R30: 22k; R_0603_1608Metric
R31: 47k; R_0603_1608Metric
R35: 100; R_0603_1608Metric
SW1: SW_ESP_BOOT_MODE; SW_Push_1P1T_XKB_TS-1187A
SW2: SW_ESP_RESET; SW_Push_1P1T_XKB_TS-1187A
SW3: SW_DOWN; SW_Push_1P1T_XKB_TS-1187A
SW4: SW_ENTER; SW_Push_1P1T_XKB_TS-1187A
SW5: SW_UP; SW_Push_1P1T_XKB_TS-1187A
SW6: SW_BACK; SW_Push_1P1T_XKB_TS-1187A
SW7: PWR; SS-12D07-VG 4 NS GA PA
TP1: TP_ISENSE; TestPoint_Pad_1.0x1.0mm
TP2: TP_GND; TestPoint_Pad_1.0x1.0mm
TP3: TP_3V3; TestPoint_Pad_1.0x1.0mm
TP4: TP_VPSU; TestPoint_Pad_1.0x1.0mm
TP5: TP_VUSB; TestPoint_Pad_1.0x1.0mm
TP6: B_SENSE; TestPoint_Pad_1.0x1.0mm
TP7: TP_MUX; TestPoint_Pad_1.0x1.0mm
TP8: TP_BTN; TestPoint_Pad_1.0x1.0mm
TP9: IO42; TestPoint_Pad_1.0x1.0mm
TP10: IO41; TestPoint_Pad_1.0x1.0mm
TP11: IO40; TestPoint_Pad_1.0x1.0mm
TP12: IO39; TestPoint_Pad_1.0x1.0mm
TP13: TP_SCL; TestPoint_Pad_1.0x1.0mm
TP14: TP_SDA; TestPoint_Pad_1.0x1.0mm
TP15: I2S_LRCLK; TestPoint_Pad_1.0x1.0mm
TP16: I2S_BLCK; TestPoint_Pad_1.0x1.0mm
TP17: GPS_RX; TestPoint_Pad_1.0x1.0mm
TP18: GPS_TX; TestPoint_Pad_1.0x1.0mm
TP19: GPS_RST; TestPoint_Pad_1.0x1.0mm
TP20: 5V_RAW; TestPoint_Pad_1.0x1.0mm
TP21: PSU_EN; TestPoint_Pad_1.0x1.0mm
TP22: I2S_DIN; TestPoint_Pad_1.0x1.0mm
TP23: CHRG_STAT; TestPoint_Pad_1.0x1.0mm
TP24: IO4; TestPoint_Pad_1.0x1.0mm
TP25: IO45; TestPoint_Pad_1.0x1.0mm
TP26: ADC_LDO; TestPoint_Pad_1.0x1.0mm
U1: CP2102N-Axx-xQFN28; QFN-28-1EP_5x5mm_P0.5mm_EP3.35x3.35mm
U2: ESP32-S3-WROOM-1
U3: RFM95W-915S2; RFM95W
U4: ACS70331EOLC; SOIC127P600X175-8N
U5, U6: LM66100DCKR; SC-70-6_Handsoldering
U7: MAX98357AETE_T; MAX98357_QFN50P300X300X80-17N
U8: TPS63001DRCR; Texas_DRC0010J_ThermalVias
U9: YIC31616GMSGG GPS; YIC31616GMSGG
U10: TPB4056B2X-ES1R; ES1ESOP-8-F_TPK
U11: AMS1117-3.3; SOT-223-3_TabPin2
U12: NAU7802SGI; SOI16_NAU7802SGI_NUV

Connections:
5V_OFF: R38.1, R39.1, U2.15 (GPIO3/TOUCH3/ADC1_CH2)
5V_RAW: C26.2, J1.A4 (VBUS), J1.A9 (VBUS), J1.B4 (VBUS), J1.B9 (VBUS), Q3.2 (S), R9.1, R10.1, R30.2, TP20.1
+3.3V: C5.2, C6.2, C9.1, C10.1, C11.1, C12.1, C13.1, C19.2, C24.1, C25.1, C31.2, IC1.8 (VCC), J2.6 (VSS), J3.1 (VCC), J6.4, J7.4, JP2.3 (B), JP6.1 (A), R1.2, R2.2, R4.2, R11.1, R20.1, R21.1, R22.1, R23.1, R24.2, R25.1, R27.2, R32.1, TP3.1, U1.6 (VDD), U1.7 (VREGIN), U2.2 (3V3), U3.13 (3.3V), U4.3 (IP-), U4.4 (IP-), U7.7 (VDD), U7.8 (VDD__1), U9.4 (VCC), U12.15 (DVDD)
+3.3VA: C7.2, C8.2, D1.1 (VDD), D4.1 (VDD), D5.1 (VDD), D6.1 (VDD), D7.1 (VDD), J8.4, J9.4, SW3.1, SW4.1, SW5.1, SW6.1
+5V: C14.1, C16.2, C17.1, Q3.3 (D), Q6.1 (G), R36.1, U10.4 (VIN), U10.8 (CE), U11.3 (VI)
+BATT: C29.1, Q1.2 (S), R17.1, R35.1, U8.5 (VIN)
/LA: L1.2, U8.2 (L2)
/LB: L1.1, U8.4 (L1)
ARGB_DATA: J7.3, JP5.1 (A), U2.16 (GPIO46)
ARGB_DATA_DB: D1.4 (DIN), J9.3
BATT_SENSE: R16.1, R17.2, TP6.1, U12.3 (VIN1P)
BUTTONS: J7.1, U2.39 (GPIO1/TOUCH1/ADC1_CH0)
BUTTONS_DB: J9.1, R12.2, R13.2, R14.1, R15.2, R28.2, TP8.1
CHRG_STAT: R26.2, R27.1, TP23.1, U2.38 (GPIO2/TOUCH2/ADC1_CH1), U10.7 (CHRG)
CLK_SDMMC: J2.5 (CLK), R23.2, U2.29 (SPIIO7/GPIO36/FSPICLK/SUBSPICLK)
CMD_SDMMC: J2.3 (CMD), R21.2, U2.28 (SPIIO6/GPIO35/FSPID/SUBSPID)
CS_EINK: J3.5 (CS), U2.19 (GPIO11/TOUCH11/ADC2_CH0/FSPID/FSPIIO5/S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)
CS_RF: U2.8 (GPIO15/U0RTS/ADC2_CH4/XTAL_32K_P), U3.5 (NSS)
CURR_SENSE: TP1.1, U4.7 (VOUT), U12.5 (VIN2P)
D0_SDMMC: J2.7 (DAT0), R22.2, U2.30 (SPIDQS/GPIO37/FSPIQ/SUBSPIQ)
DIO0_RF: U2.5 (GPIO5/TOUCH5/ADC1_CH4), U3.14 (DIO0)
DIO1_RF: U2.6 (GPIO6/TOUCH6/ADC1_CH5), U3.15 (DIO1)
DIO2_RF: JP1.2 (B), TP24.1, U2.4 (GPIO4/TOUCH4/ADC1_CH3)
DTR: Q5.2 (E), R33.1, U1.28 (~DTR)
EINK_BUSY: J3.8 (BUSY), TP11.1, U2.33 (MTDO/GPIO40/CLK_OUT2)
EINK_DC: J3.6 (DC), U2.18 (GPIO10/TOUCH10/ADC1_CH9/FSPICS0/FSPIIO4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)
ESP32_EN: C22.2, C23.2, Q2.3 (C), R32.2, SW2.2, U2.3 (EN)
GND: AE1.2 (Shield), C1.2, C2.2, C3.2, C4.2, C5.1, C6.1, C9.2, C10.2, C11.2, C12.2, C13.2, C14.2, C15.1, C16.1, C17.2, C18.2, C19.1, C20.1, C21.1, C22.1, C23.1, C24.2, C25.2, C26.1, C27.2, C28.2, C29.2, C30.2, C31.1, D2.1 (K), D3.1 (K), IC1.4 (GND), IC1.5 (A2), IC1.6 (A1), IC1.7 (A0), J1.A1 (GND), J1.A12 (GND), J1.B1 (GND), J1.B12 (GND), J2.4 (VDD), J2.10 (SHIELD), J3.2 (GND), J4.1, J6.2, J7.2, JP2.1 (A), Q1.1 (G), Q4.2 (S), Q7.2 (S), R5.2, R6.2, R7.1, R8.2, R16.2, R29.2, R31.1, R36.2, R37.1, R38.2, SW1.1, SW2.1, TP2.1, U1.3 (GND), U1.29 (GND), U2.1 (GND), U2.40 (GND), U2.41 (GND), U3.1 (GND), U3.8 (GND), U3.10 (GND), U4.5 (GND), U5.2 (GND), U5.5 (ST), U6.2 (GND), U6.5 (ST), U7.3 (GND), U7.11 (GND__1), U7.15 (GND__2), U7.17 (EP), U8.3 (PGND), U8.9 (GND), U8.11 (PGND), U9.3 (GND), U9.12 (GND), U10.1 (TEMP), U10.3 (GND), U10.9 (GND), U11.1 (GND), U12.2 (VIN1N), U12.4 (VIN2N), U12.7 (REFN), U12.8 (AVSS), U12.9 (DVSS)
GND2: C7.1, C8.1, D1.3 (VSS), D4.3 (VSS), D5.3 (VSS), D6.3 (VSS), D7.3 (VSS), J8.2, J9.2, R28.1
GPIO0: C21.2, Q5.3 (C), SW1.2, U2.27 (GPIO0/BOOT)
GPS_RST: R11.2, TP19.1, U2.12 (GPIO8/TOUCH8/ADC1_CH7/SUBSPICS1), U9.10 (RESET)
I2C_SCL: IC1.2 (SCL), R24.1, TP13.1, U2.24 (GPIO47/SPICLK_P/SUBSPICLK_P_DIFF), U12.13 (SCLK)
I2C_SDA: IC1.1 (SDA), R25.2, TP14.1, U2.25 (GPIO48/SPICLK_N/SUBSPICLK_N_DIFF), U12.14 (SDIO)
I2S_BCLK_SPK: TP16.1, U2.31 (GPIO38/FSPIWP/SUBSPIWP), U7.16 (BCLK)
I2S_DIN_SPK: JP3.2 (B), TP22.1, U2.23 (GPIO21)
I2S_LRCLK_SPK: TP15.1, U2.22 (GPIO14/TOUCH14/ADC2_CH3/FSPIWP/FSPIDQS/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), U7.14 (LRCLK)
MISO_EINK: TP9.1, U2.35 (MTMS/GPIO42)
MISO_RF: U2.11 (GPIO18/U1RXD/ADC2_CH7/CLK_OUT3), U3.2 (MISO)
MOSI_EINK: J3.3 (DIN), U2.21 (GPIO13/TOUCH13/ADC2_CH2/FSPIQ/FSPIIO7/S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)
MOSI_RF: U2.10 (GPIO17/U1TXD/ADC2_CH6), U3.3 (MOSI)
unnamed: AE1.1 (A), U3.9 (ANT)
unnamed: D1.2 (DOUT), D4.4 (DIN)
unnamed: D2.2 (A), R2.1
unnamed: D3.2 (A), R3.1
unnamed: D4.2 (DOUT), D5.4 (DIN)
unnamed: D5.2 (DOUT), D6.4 (DIN)
unnamed: D6.2 (DOUT), D7.4 (DIN)
unnamed: J1.A5 (CC1), R5.1
unnamed: J1.B5 (CC2), R6.1
unnamed: J2.2 (DAT3/CD), R20.2
unnamed: J5.1, U7.10 (OUTN)
unnamed: J5.2, U7.9 (OUTP)
unnamed: JP1.1 (A), U3.16 (DIO2)
unnamed: JP2.2 (C), U7.2 (GAIN_SLOT)
unnamed: JP3.1 (A), U7.1 (DIN)
unnamed: JP4.1 (A), R8.1
unnamed: JP4.2 (B), R7.2, U10.2 (PROG)
unnamed: JP5.2 (B), R3.2
unnamed: JP6.2 (B), U12.1 (REFP)
unnamed: Q1.3 (D), SW7.1 (A)
unnamed: Q2.1 (B), R33.2
unnamed: Q3.1 (G), Q4.3 (D), R10.2
unnamed: Q4.1 (G), Q7.3 (D), R9.2
unnamed: Q5.1 (B), R34.1
unnamed: Q6.3 (D), R37.2, TP21.1, U8.6 (EN)
unnamed: C30.1, Q6.2 (S), R35.2, U8.7 (PS/SYNC), U8.8 (VINA)
unnamed: Q7.1 (G), R39.2
unnamed: R12.1, SW5.2
unnamed: R13.1, SW3.2
unnamed: R14.2, SW6.2
unnamed: R15.1, SW4.2
unnamed: C20.2, R30.1, R31.2, U1.8 (VBUS)
unnamed: R29.1, U1.9 (~RST)
unnamed: TP25.1, U2.26 (GPIO45)
unnamed: TP12.1, U2.32 (MTCK/GPIO39/CLK_OUT3/SUBSPICS1)
unnamed: R18.2, U7.4 (SD_MODE)
unnamed: R26.1, U10.6 (STBY)
unnamed: TP26.1, U12.16 (AVDD/LDO)
RAW_BATT: C15.2, J4.2, SW7.2 (B), U10.5 (BAT)
RESET_EINK: J3.7 (RST), U2.17 (GPIO9/TOUCH9/ADC1_CH8/FSPIHD/SUBSPIHD)
RESET_RF: R1.1, U2.7 (GPIO7/TOUCH7/ADC1_CH6), U3.6 (RESET)
RTS: Q2.2 (E), R34.2, U1.24 (~RTS)
SCK_EINK: J3.4 (CLK), U2.20 (GPIO12/TOUCH12/ADC2_CH1/FSPICLK/FSPIIO6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)
SCK_RF: U2.9 (GPIO16/U0CTS/ADC2_CH5/XTAL_32K_N), U3.4 (SCK)
SPK_ON: R18.1, TP10.1, U2.34 (MTDI/GPIO41/CLK_OUT1)
UART0_RX: U1.26 (TXD), U2.36 (U0RXD/GPIO44/CLK_OUT2)
UART0_TX: U1.25 (RXD), U2.37 (U0TXD/GPIO43/CLK_OUT1)
UART1_GPS_RX: TP18.1, U2.13 (GPIO19/U1RTS/ADC2_CH8/CLK_OUT2/USB_D-), U9.2 (TXD)
UART1_GPS_TX: TP17.1, U2.14 (GPIO20/U1CTS/ADC2_CH9/CLK_OUT1/USB_D+), U9.1 (RXD)
USB_D+: J1.A6 (D+), J1.B6 (D+), R4.1, U1.4 (D+)
USB_D-: J1.A7 (D-), J1.B7 (D-), U1.5 (D-)
V_MUX: C1.1, C2.1, TP7.1, U4.1 (IP+), U4.2 (IP+), U4.8 (VCC), U5.3 (*CE), U5.6 (VOUT), U6.3 (*CE), U6.6 (VOUT)
V_PSU: C4.1, C27.1, C28.1, TP4.1, U6.1 (VIN), U8.1 (VOUT), U8.10 (FB)
V_REGUSB: C3.1, C18.1, TP5.1, U5.1 (VIN), U11.2 (VO)

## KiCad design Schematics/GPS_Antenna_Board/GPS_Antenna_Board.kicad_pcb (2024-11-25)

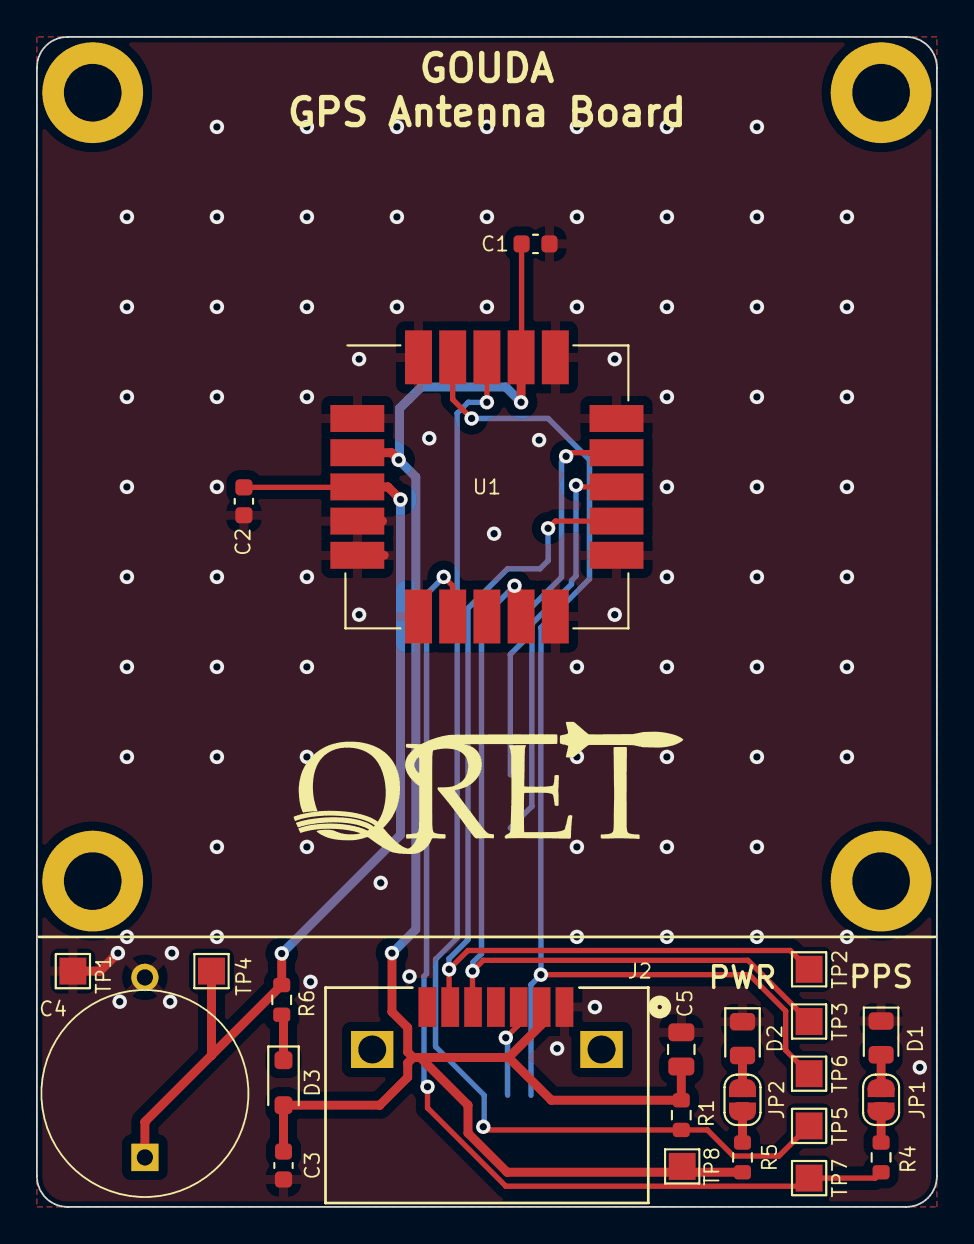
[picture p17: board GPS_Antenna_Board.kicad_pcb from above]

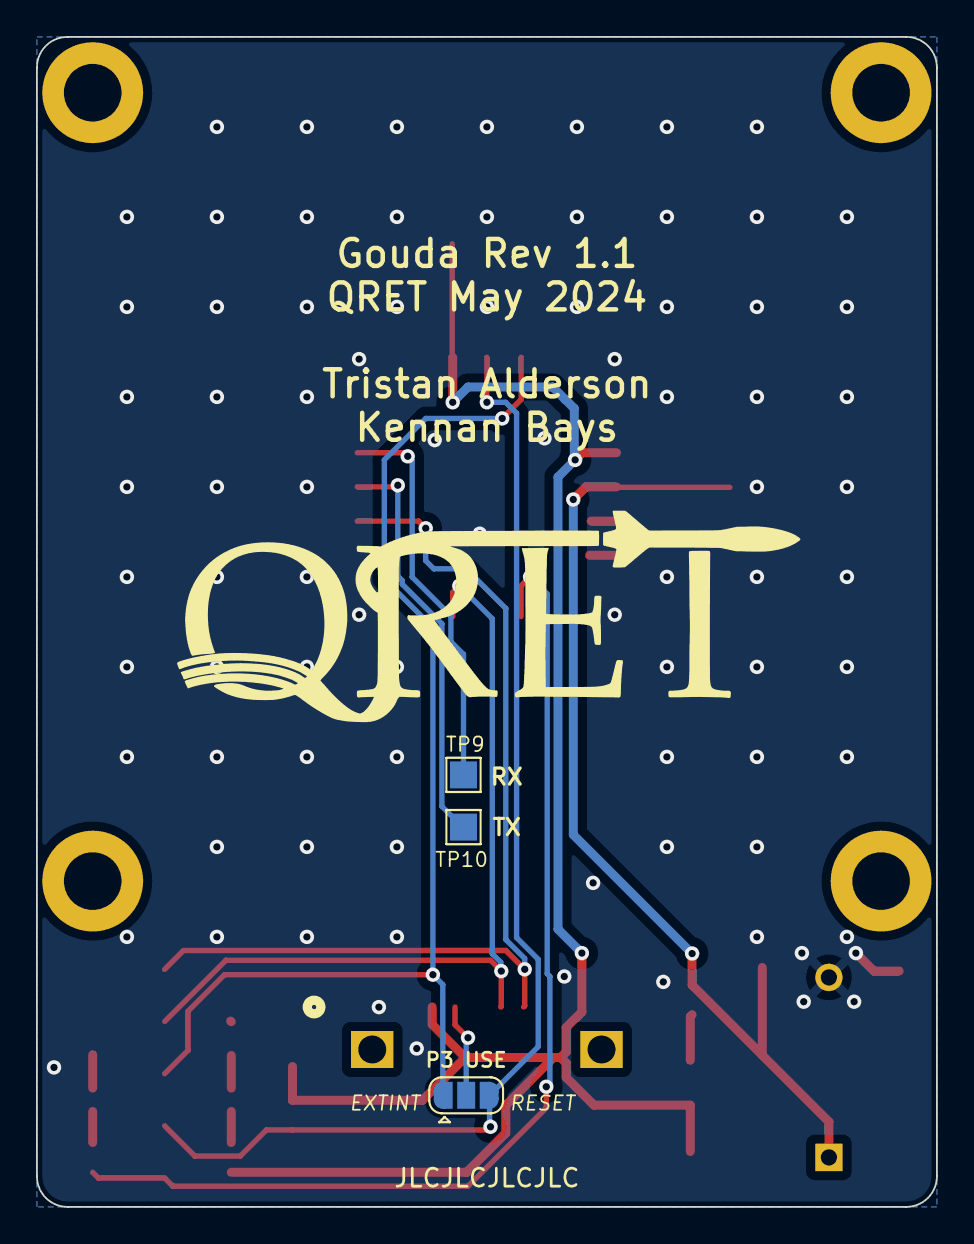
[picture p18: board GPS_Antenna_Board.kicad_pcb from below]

Board: 2 copper layers, 50.0 x 65.0 mm, 31 parts (3 on the bottom side), 16 nets.

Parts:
C1, C2: 100nF; C_0603_1608Metric
C3: 1uF; C_0603_1608Metric
C4: 330mF; CB5R5334HF-ZJP
C5: 47uF; C_0805_2012Metric
D1: White; LED_0805_2012Metric
D2: Green; LED_0805_2012Metric
D3: 1N5819WS; D_SOD-323_HandSoldering
H1, H2, H3, H4: MountingHole; MountingHole_3.2mm_M3_DIN965_Pad
J2: SATA Conn. (Male); CONN_47080-4001_MOL_SATA
JP1: ENA_PPS_LED; SolderJumper-2_P1.3mm_Open_RoundedPad1.0x1.5mm
JP2: ENA_PWR_LED; SolderJumper-2_P1.3mm_Open_RoundedPad1.0x1.5mm
JP3: P3 FUNC; SolderJumper-3_P1.3mm_Open_RoundedPad1.0x1.5mm
R1: 10k; R_0603_1608Metric
R4: 2.2k; R_0603_1608Metric
R5: 3.3k; R_0603_1608Metric
R6: 100R; R_0603_1608Metric
TP1: TP_GND; TestPoint_Pad_1.5x1.5mm
TP2: TP_SCL; TestPoint_Pad_1.5x1.5mm
TP3: TP_SDA; TestPoint_Pad_1.5x1.5mm
TP4: TP_BCKP; TestPoint_Pad_1.5x1.5mm
TP5: TP_RST; TestPoint_Pad_1.5x1.5mm
TP6: TP_INT; TestPoint_Pad_1.5x1.5mm
TP7: TP_PPS; TestPoint_Pad_1.5x1.5mm
TP8: TP_3.3V; TestPoint_Pad_1.5x1.5mm
TP9: RX; TestPoint_Pad_1.5x1.5mm
TP10: TX; TestPoint_Pad_1.5x1.5mm
U1: SAM-M10Q; ublox_SAM-M8Q_HandSolder

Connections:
+3.3V: C1.2, C3.1, C5.1, D3.2 (A), J2.2, R1.1, R5.1, TP8.1, U1.2 (VCC_IO), U1.17 (VCC)
BCKP_BATT: C2.2, C4.1, R6.2, TP4.1, U1.3 (V_BCKP)
GND: C1.1, C2.1, C3.2, C4.2, C5.2, D1.1 (K), D2.1 (K), J2.1, TP1.1, U1.1 (GND), U1.4 (GND), U1.5 (GND), U1.6 (GND), U1.10 (GND), U1.11 (GND), U1.15 (GND), U1.16 (GND), U1.20 (GND)
GPS_EXTINT: JP3.1 (A), TP6.1, U1.19 (EXTINT)
GPS_PPS: R4.1, TP7.1, U1.7 (TIMEPULSE)
GPS_RST: JP3.3 (B), R1.2, TP5.1, U1.18 (~RESET)
unnamed: D1.2 (A), JP1.1 (A)
unnamed: D2.2 (A), JP2.1 (A)
unnamed: D3.1 (K), R6.1
unnamed: JP1.2 (B), R4.2
unnamed: JP2.2 (B), R5.2
unnamed: J2.3, JP3.2 (C)
unnamed: TP9.1, U1.14 (RXD)
unnamed: TP10.1, U1.13 (TXD)
SCL: J2.6, TP2.1, U1.12 (SCL)
SDA: J2.5, TP3.1, U1.9 (SDA)

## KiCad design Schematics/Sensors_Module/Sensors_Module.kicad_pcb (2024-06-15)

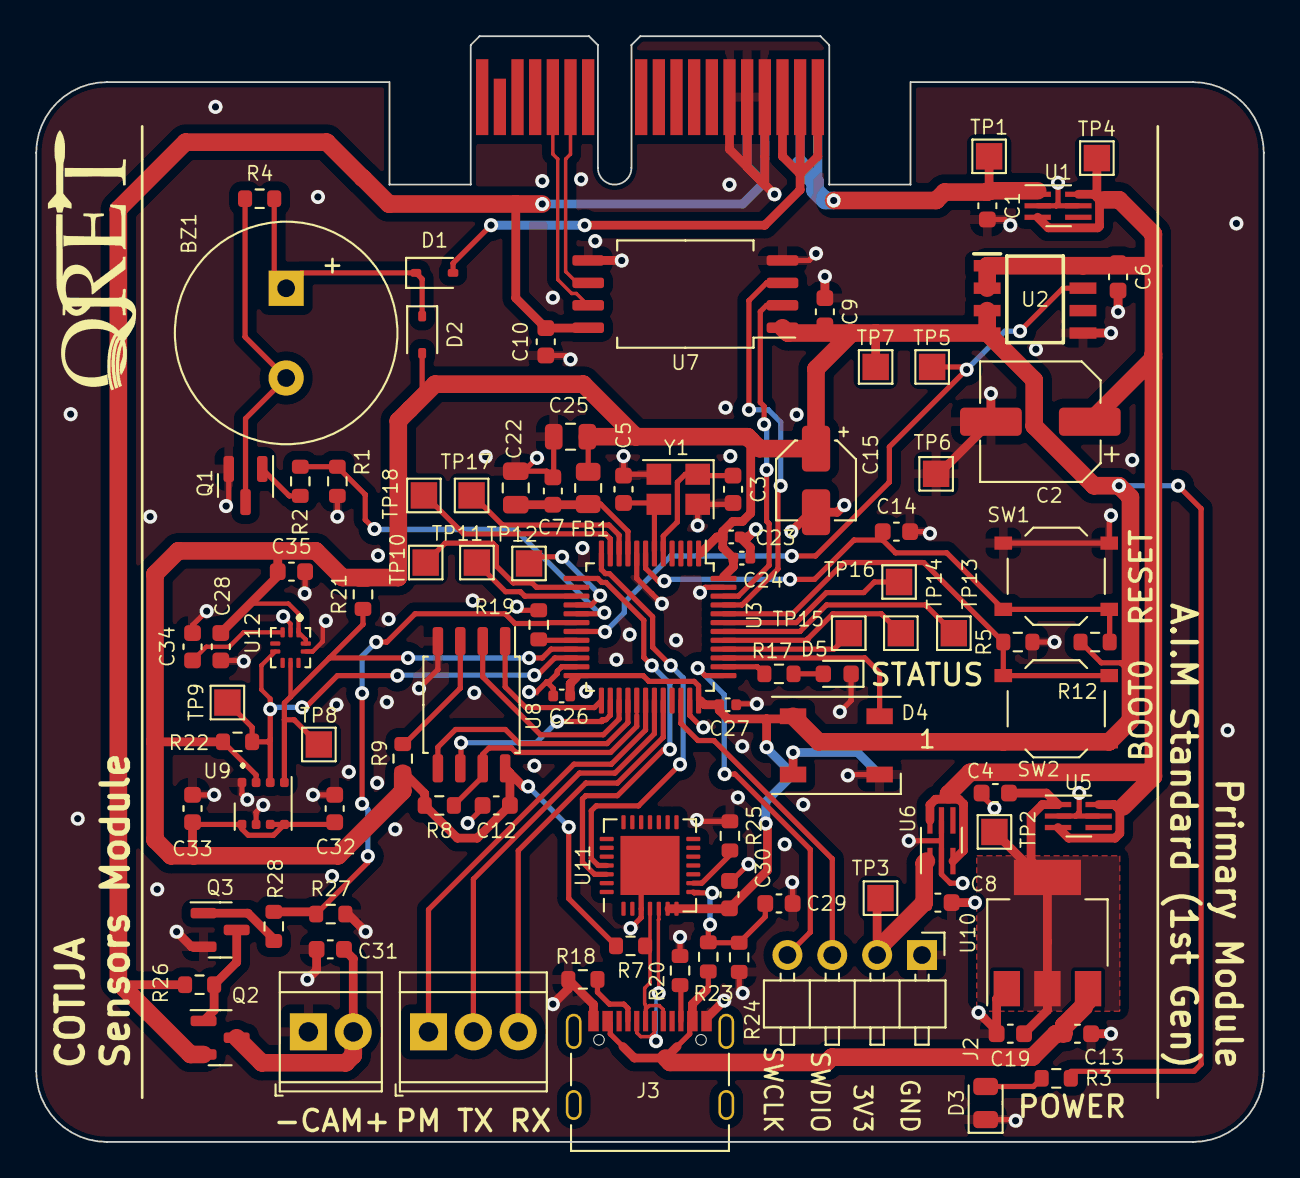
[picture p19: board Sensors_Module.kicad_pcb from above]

Board: 2 copper layers, 69.5 x 62.6 mm, 98 parts (1 on the bottom side), 64 nets.

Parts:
BZ1: PKM13EPYH4000; Buzzer_12.6x9.5RM5.0
C1, C4, C8, C28, C29, C34, C35: 1uF; C_0603_1608Metric
C2: 100uF; CP_Elec_6.3x5.9
C3, C5: 10p; C_0603_1608Metric
C6: 0.1uF; C_0603_1608Metric
C7: 10n; C_0603_1608Metric
C9, C10: 0.1u; C_0603_1608Metric
C12, C14, C32, C33: 100nF; C_0603_1608Metric
C13, C19, C30, C31: 10uF; C_0603_1608Metric
C15: 10uF; CP_Elec_4x5.4
C22, C25: 1uF; C_0805_2012Metric
C23, C24, C26, C27: 100n; C_0402_1005Metric
D1, D2: 1N5819WS; D_SOD-323
D3: PWR_LED (GRN); LED_0805_2012Metric
D4, D6: WS2812B; LED_WS2812B_PLCC4_5.0x5.0mm_P3.2mm
D5: DB_LED (YLW); LED_0603_1608Metric
FB1: 100R; R_0805_2012Metric
J1: Stack Male Edge Connector; BUS_PCIexpress_x1
J2: SWD_01x04_Pin; SWD_PinHeader_1x04_P2.54mm_Horizontal
J3: USB_C_Female_USB2_Small; USB_C_DB-108PWB
J6: CAM_PWR; TerminalBlock_TE_282834-2_1x02_P2.54mm_Horizontal
J7: CAM_DAT; TerminalBlock_TE_282834-3_1x03_P2.54mm_Horizontal
Q1, Q3: AO3400A; SOT-23
Q2: AO3401A; SOT-23
R1, R8, R9, R12: 10k; R_0603_1608Metric
R2: 510R; R_0603_1608Metric
R3: 3.3k; R_0603_1608Metric
R4, R25: 1k; R_0603_1608Metric
R5, R19, R26, R27: 100k; R_0603_1608Metric
R7: 1.5k; R_0603_1608Metric
R17: 680R; R_0603_1608Metric
R18, R20: 5.1k; R_0603_1608Metric
R21, R22: 4.7k; R_0603_1608Metric
R23: 22k; R_0603_1608Metric
R24: 47k; R_0603_1608Metric
R28: 510; R_0603_1608Metric
SW1: SW_STM_RESET; SW_Push_1P1T_XKB_TS-1187A
SW2: SW_STM_BOOT_MODE; SW_Push_1P1T_XKB_TS-1187A
TP1: TP_VSTACK; TestPoint_Pad_1.5x1.5mm
TP2: TP_VUSB; TestPoint_Pad_1.5x1.5mm
TP3: TP_VSWD; TestPoint_Pad_1.5x1.5mm
TP4: TP_MUX; TestPoint_Pad_1.5x1.5mm
TP5: TP_ISENSE; TestPoint_Pad_1.5x1.5mm
TP6: TP_GND; TestPoint_Pad_1.5x1.5mm
TP7: TP_3V3; TestPoint_Pad_1.5x1.5mm
TP8: TP_SCL; TestPoint_Pad_1.5x1.5mm
TP9: TP_SDA; TestPoint_Pad_1.5x1.5mm
TP10: PA4; TestPoint_Pad_1.5x1.5mm
TP11: PA5; TestPoint_Pad_1.5x1.5mm
TP12: PA6; TestPoint_Pad_1.5x1.5mm
TP13: PB6; TestPoint_Pad_1.5x1.5mm
TP14: PB5; TestPoint_Pad_1.5x1.5mm
TP15: PB4; TestPoint_Pad_1.5x1.5mm
TP16: PB7; TestPoint_Pad_1.5x1.5mm
TP17: PA0; TestPoint_Pad_1.5x1.5mm
TP18: PA1; TestPoint_Pad_1.5x1.5mm
U1, U5, U6: LM66100DCKR; SC-70-6_Handsoldering
U2: ACS70331EOLC; SOIC127P600X175-8N
U3: STM32F103CBT6; LQFP-48_7x7mm_P0.5mm
U7: ISO1042BDWVR; SOIC-8 ISO1042BDWV
U8: W25Q128JVS; SOIC-8_5.23x5.23mm_P1.27mm
U9: BME680; Bosch_LGA-8_3x3mm_P0.8mm_ClockwisePinNumbering
U10: AMS1117-3.3; SOT-223-3_TabPin2
U11: CP2102N-Axx-xQFN28; QFN-28-1EP_5x5mm_P0.5mm_EP3.35x3.35mm
U12: BM1422AGMV; Rohm_MLGA010V020A_LGA-10_2x2mm_P0.45mm_LayoutBorder_3x2y
Y1: X322516MMB4SI; Crystal_SMD_3225-4Pin_3.2x2.5mm

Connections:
5V_RAW: C13.1, J3.A4 (VBUS), J3.A9 (VBUS), J3.B4 (VBUS), J3.B9 (VBUS), R23.2, U10.3 (VI)
+3.3V: C9.2, C12.1, C15.1, C23.1, C24.1, C25.1, C26.1, C27.1, C28.1, C30.2, C32.1, C33.1, C35.1, D2.2 (A), D4.1 (VDD), D6.1 (VDD), FB1.2, R3.2, R7.1, R8.2, R9.2, R12.2, R21.1, R22.2, SW2.2, TP7.1, U2.3 (IP-), U2.4 (IP-), U3.1 (VBAT), U3.24 (VDD), U3.36 (VDD), U3.48 (VDD), U7.1 (VCC1), U8.8 (VCC), U9.2 (CSB), U9.5 (SDO), U9.6 (VDDIO), U9.8 (VDD), U11.6 (VDD), U11.7 (VREGIN), U12.1 (AVDD), U12.10 (DVDD)
+3.3VA: C7.1, C22.1, FB1.1, U3.9 (VDDA)
+5V: C10.2, J1.A4 (5.0V_A), J1.A5 (5.0V_A), Q2.2 (S), R26.1, U7.8 (VCC2)
+BATT: D1.2 (A), J1.B1 (BATT_A), J1.B2 (BATT_A), J1.B3 (BATT_A)
BOOT0: R5.2, SW2.1, U3.44 (BOOT0)
BOOT1: R19.2, U3.20 (PB2)
BUZZER: R1.2, R2.2, U3.17 (PA7)
CAM_5V: C31.1, J6.2, Q2.3 (D)
CAM_PWM: J7.3, U3.32 (PA11)
CAM_PWR: R27.1, R28.1, U3.18 (PB0)
CAM_RX: J7.2, U3.31 (PA10)
CAM_TX: J7.1, U3.30 (PA9)
CAN_H: J1.B14 (CAN_H), U7.7 (CANH)
CAN_L: J1.B13 (CAN_L), U7.6 (CANL)
CAN_RX: U3.45 (PB8), U7.3 (RXD)
CAN_TX: U3.46 (PB9), U7.2 (TXD)
CS_FL: U3.25 (PB12), U8.1 (~CS)
CURR_SENSE: TP5.1, U2.7 (VOUT), U3.19 (PB1)
DB_LED: R17.2, U3.38 (PA15)
GND: C1.2, C2.2, C3.2, C4.2, C5.2, C6.2, C7.2, C8.2, C9.1, C10.1, C12.2, C13.2, C14.2, C15.2, C19.2, C22.2, C23.2, C24.2, C25.2, C26.2, C27.2, C28.2, C29.1, C30.1, C31.2, C32.2, C33.2, C34.2, C35.2, D3.1 (K), D4.3 (VSS), D5.1 (K), D6.3 (VSS), J1.A3 (GND_A), J1.A6 (GND_A), J1.B4 (GND_A), J1.B5 (GND_A), J1.B6 (GND_A), J2.1 (GND), J3.A1 (GND), J3.A12 (GND), J3.B1 (GND), J3.B12 (GND), J6.1, Q1.2 (S), Q3.2 (S), R1.1, R5.1, R18.2, R19.1, R20.2, R24.1, R25.2, R27.2, SW1.1, TP6.1, U1.2 (GND), U1.5 (ST), U2.5 (GND), U3.8 (VSSA), U3.23 (VSS), U3.35 (VSS), U3.47 (VSS), U5.2 (GND), U5.5 (ST), U6.2 (GND), U6.5 (ST), U7.4 (GND1), U7.5 (GND2), U8.4 (GND), U9.1 (GND), U9.7 (GND), U10.1 (GND), U11.3 (GND), U11.29 (GND), U12.2 (GND), U12.9 (ADDR), Y1.2, Y1.4
MISO_FL: U3.27 (PB14), U8.2 (DO(IO1))
MOSI_FL: U3.28 (PB15), U8.5 (DI(IO0))
unnamed: BZ1.2 (+), Q1.3 (D), R4.1
unnamed: BZ1.1 (-), D1.1 (K), D2.1 (K), R4.2
unnamed: D3.2 (A), R3.1
unnamed: D4.2 (DOUT), D6.4 (DIN)
unnamed: D5.2 (A), R17.1
unnamed: J3.A5 (CC1), R18.1
unnamed: J3.B5 (CC2), R20.1
unnamed: Q1.1 (G), R2.1
unnamed: Q2.1 (G), Q3.3 (D), R26.2
unnamed: Q3.1 (G), R28.2
unnamed: TP17.1, U3.10 (PA0)
unnamed: TP18.1, U3.11 (PA1)
unnamed: TP10.1, U3.14 (PA4)
unnamed: TP11.1, U3.15 (PA5)
unnamed: TP12.1, U3.16 (PA6)
unnamed: TP15.1, U3.40 (PB4)
unnamed: TP14.1, U3.41 (PB5)
unnamed: TP13.1, U3.42 (PB6)
unnamed: TP16.1, U3.43 (PB7)
unnamed: R9.1, U8.3 (IO2)
unnamed: C29.2, R23.1, R24.2, U11.8 (VBUS)
unnamed: R25.1, U11.9 (~RST)
unnamed: C34.1, U12.3 (VREG)
OSC_IN: C3.1, U3.5 (PD0), Y1.1
OSC_OUT: C5.1, U3.6 (PD1), Y1.3
RESET_FL: R8.1, U3.29 (PA8), U8.7 (IO3)
RGB_DATA: D4.4 (DIN), U3.39 (PB3)
SCK_FL: U3.26 (PB13), U8.6 (CLK)
SCL: R21.2, TP8.1, U3.21 (PB10), U9.4 (SCK), U12.7 (SCL)
SDA: R22.1, TP9.1, U3.22 (PB11), U9.3 (SDI), U12.5 (SDA)
STM_RESET: C14.1, R12.1, SW1.2, U3.7 (NRST)
SWCLK: J2.4 (SWCLK), U3.37 (PA14)
SWDIO: J2.3 (SWDIO), U3.34 (PA13)
USB_D+: J3.A6 (D+), J3.B6 (D+), R7.2, U11.4 (D+)
USB_D-: J3.A7 (D-), J3.B7 (D-), U11.5 (D-)
USB_RX: U3.13 (PA3), U11.26 (TXD)
USB_TX: U3.12 (PA2), U11.25 (RXD)
V_MUX: C2.1, C6.1, TP4.1, U1.3 (*CE), U1.6 (VOUT), U2.1 (IP+), U2.2 (IP+), U2.8 (VCC), U5.3 (*CE), U5.6 (VOUT), U6.3 (*CE), U6.6 (VOUT)
V_PSU: C1.1, J1.A1 (3.3V_A), J1.A2 (3.3V_A), TP1.1, U1.1 (VIN)
V_REGUSB: C4.1, C19.1, TP2.1, U5.1 (VIN), U10.2 (VO)
V_SWD: C8.1, J2.2 (3V3), TP3.1, U6.1 (VIN)

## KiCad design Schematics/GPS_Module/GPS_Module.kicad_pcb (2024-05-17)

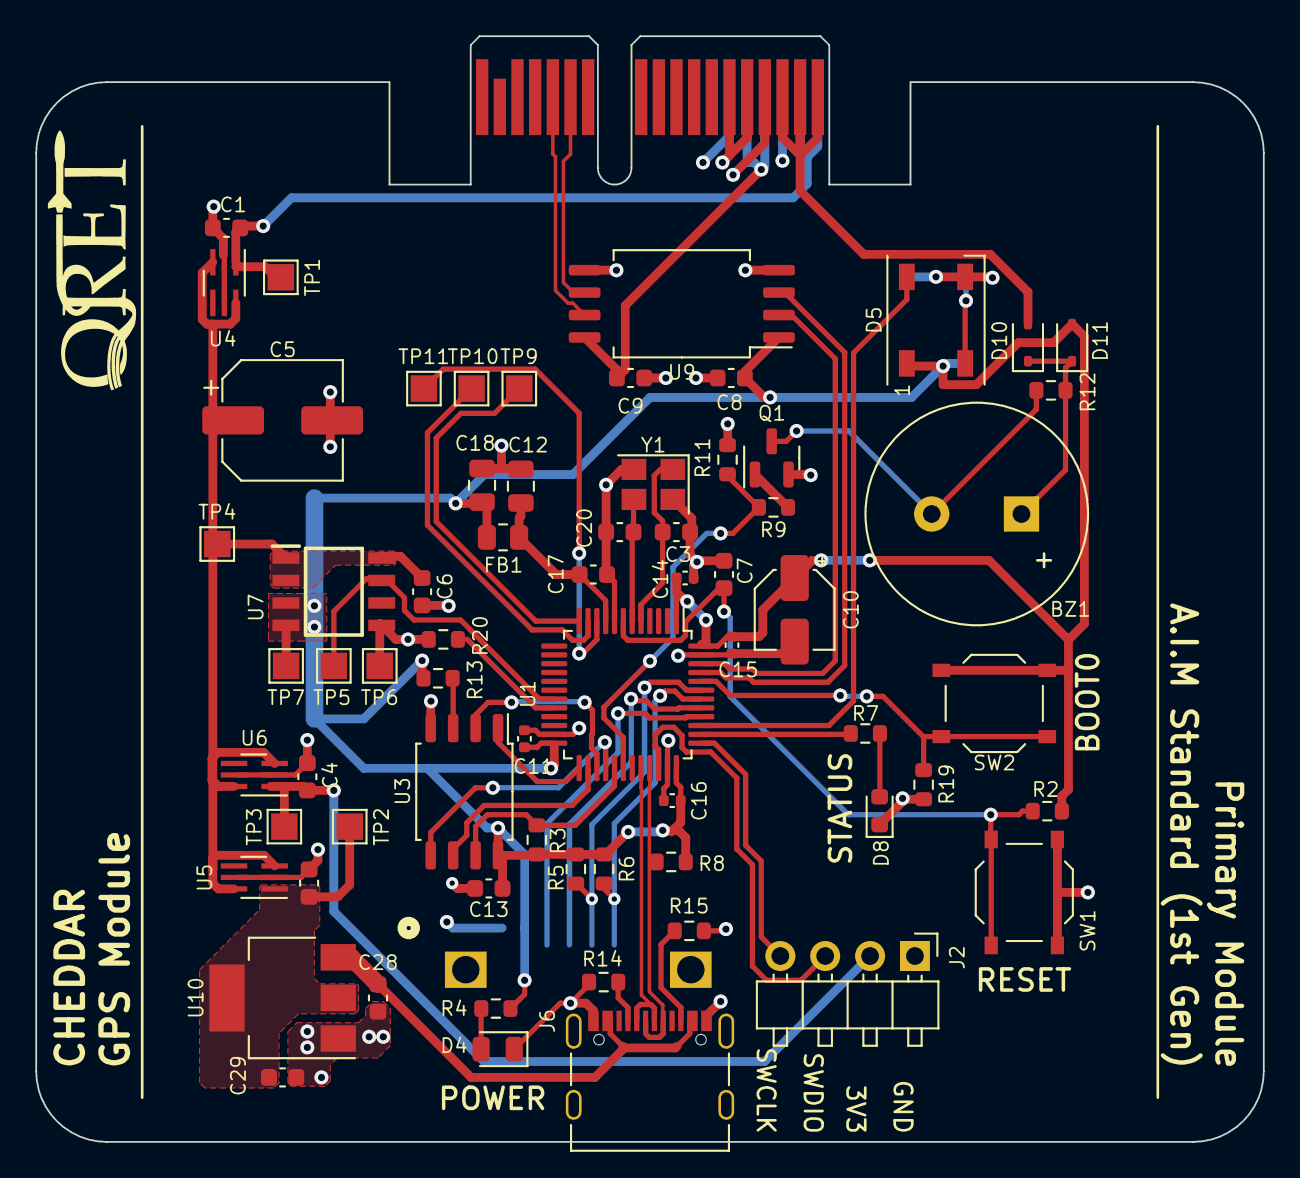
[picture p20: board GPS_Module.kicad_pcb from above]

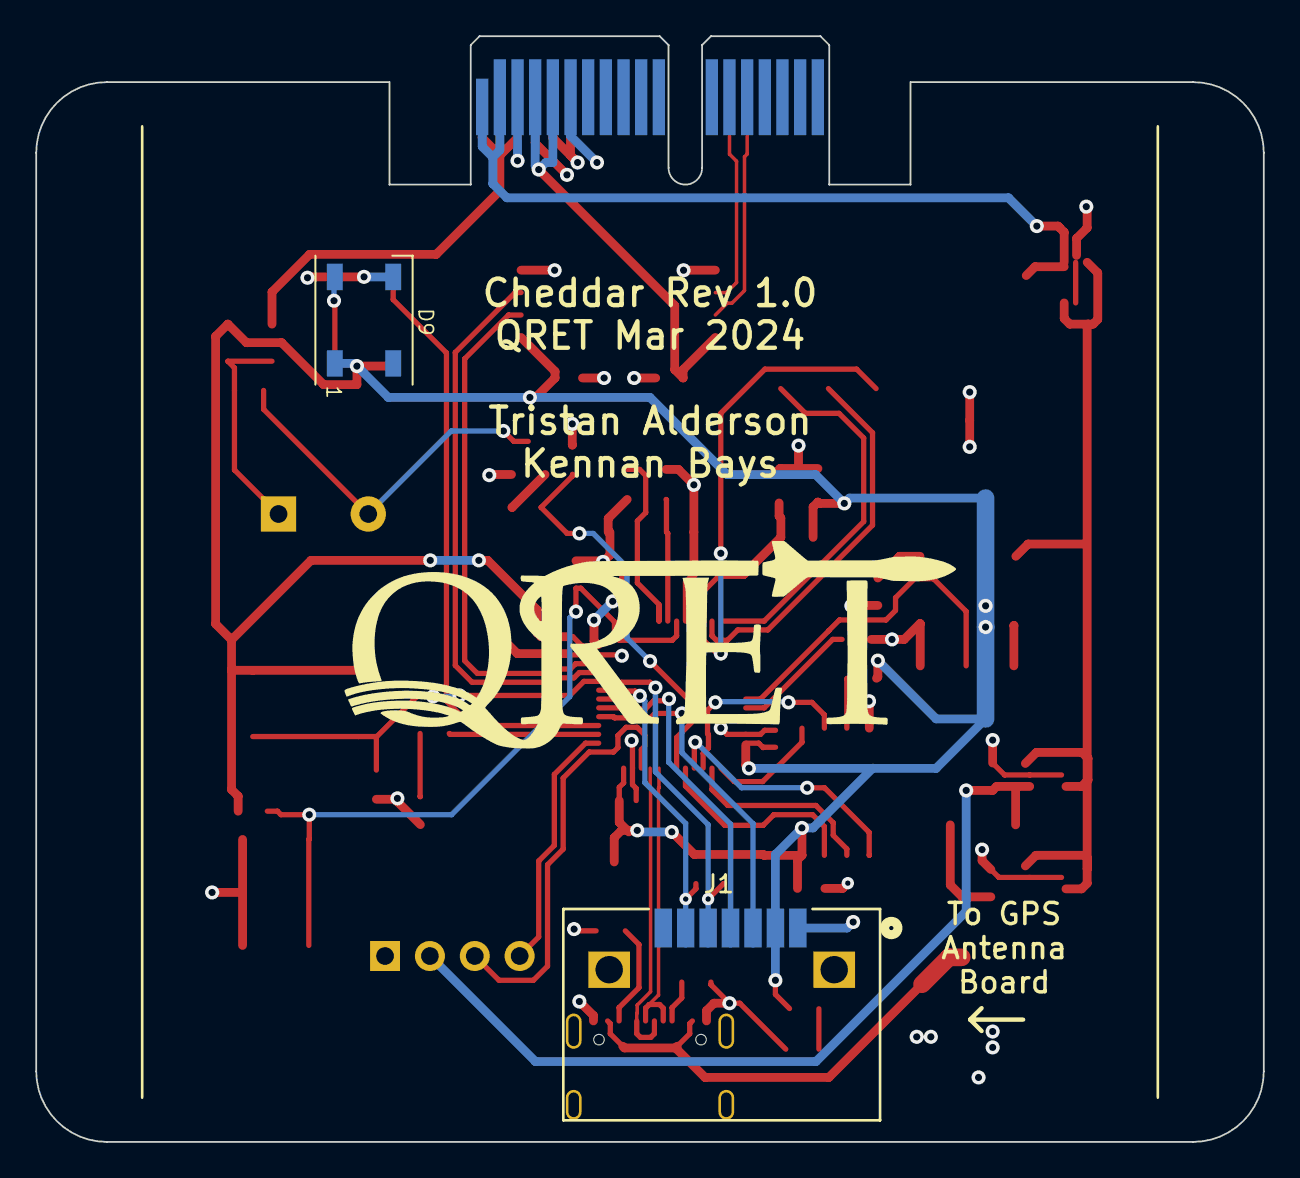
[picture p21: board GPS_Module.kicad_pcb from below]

Board: 4 copper layers, 69.5 x 62.6 mm, 70 parts (2 on the bottom side), 48 nets.

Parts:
BZ1: PKM13EPYH4000; Buzzer_12.6x9.5RM5.0
C1, C2, C4: 1uF; C_0603_1608Metric
C3, C20: 10p; C_0603_1608Metric
C5: 100uF; CP_Elec_6.3x5.9
C6: 0.1uF; C_0603_1608Metric
C7, C13: 100nF; C_0603_1608Metric
C8, C9: 0.1u; C_0603_1608Metric
C10: 10uF; CP_Elec_4x5.4
C11, C14, C15, C16: 100n; C_0402_1005Metric
C12, C18: 1uF; C_0805_2012Metric
C17: 10n; C_0603_1608Metric
C28, C29: 10uF; C_0603_1608Metric
D4: PWR_LED (GRN); LED_0805_2012Metric
D5, D9: WS2812B; LED_WS2812B_PLCC4_5.0x5.0mm_P3.2mm
D8: DB_LED (YLW); LED_0603_1608Metric
D10, D11: 1N5819WS; D_SOD-323
FB1: 100R; R_0805_2012Metric
J1: SATA Conn. (Male); CONN_47080-4001_MOL_SATA
J2: SWD_01x04_Pin; SWD_PinHeader_1x04_P2.54mm_Horizontal
J4: Stack Male Edge Connector; BUS_PCIexpress_x1
J6: USB_C_Female_USB2_Small; USB_C_DB-108PWB
Q1: AO3400A; SOT-23
R2, R3, R11, R13: 10k; R_0603_1608Metric
R4: 1.2k; R_0603_1608Metric
R5, R6: 2.2k; R_0603_1608Metric
R7: 680R; R_0603_1608Metric
R8: 1.5k; R_0603_1608Metric
R9: 510R; R_0603_1608Metric
R12: 1k; R_0603_1608Metric
R14, R15: 5.1k; R_0603_1608Metric
R19, R20: 100k; R_0603_1608Metric
SW1: SW_STM_RESET; SW_Push_1P1T_XKB_TS-1187A
SW2: SW_STM_BOOT_MODE; SW_Push_1P1T_XKB_TS-1187A
TP1: TP_VSTACK; TestPoint_Pad_1.5x1.5mm
TP2: TP_VUSB; TestPoint_Pad_1.5x1.5mm
TP3: TP_VSWD; TestPoint_Pad_1.5x1.5mm
TP4: TP_MUX; TestPoint_Pad_1.5x1.5mm
TP5: TP_ISENSE; TestPoint_Pad_1.5x1.5mm
TP6: TP_GND; TestPoint_Pad_1.5x1.5mm
TP7: TP_3V3; TestPoint_Pad_1.5x1.5mm
TP9: TP_PA2; TestPoint_Pad_1.5x1.5mm
TP10: TP_PA1; TestPoint_Pad_1.5x1.5mm
TP11: TP_PA0; TestPoint_Pad_1.5x1.5mm
U1: STM32F103CBT6; LQFP-48_7x7mm_P0.5mm
U3: W25Q128JVS; SOIC-8_5.23x5.23mm_P1.27mm
U4, U5, U6: LM66100DCKR; SC-70-6_Handsoldering
U7: ACS70331EOLC; SOIC127P600X175-8N
U9: ISO1042BQDWVR; SOIC-8 ISO1042BDWV
U10: AMS1117-3.3; SOT-223-3_TabPin2
Y1: X322516MMB4SI; Crystal_SMD_3225-4Pin_3.2x2.5mm

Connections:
+3.3V: C8.2, C10.1, C11.1, C13.1, C14.1, C15.1, C16.1, C18.1, D5.1 (VDD), D9.1 (VDD), D11.2 (A), FB1.2, J1.2, R2.2, R3.2, R4.2, R5.2, R6.1, R8.1, R13.2, SW2.2, TP7.1, U1.1 (VBAT), U1.24 (VDD), U1.36 (VDD), U1.48 (VDD), U3.8 (VCC), U7.3 (IP-), U7.4 (IP-), U9.1 (VCC1)
+3.3VA: C12.1, C17.1, FB1.1, U1.9 (VDDA)
+5V: C9.2, J4.A4 (5.0V_A), J4.A5 (5.0V_A), U9.8 (VCC2)
+BATT: D10.2 (A), J4.B1 (BATT_A), J4.B2 (BATT_A), J4.B3 (BATT_A)
/USB_5V: C28.1, J6.A4 (VBUS), J6.A9 (VBUS), J6.B4 (VBUS), J6.B9 (VBUS), U10.3 (VI)
BOOT0: R19.2, SW2.1, U1.44 (BOOT0)
BOOT1: R20.2, U1.20 (PB2)
BUZZER: R9.2, R11.2, U1.30 (PA9)
CAN_H: J4.B14 (CAN_H), U9.7 (CANH)
CAN_L: J4.B13 (CAN_L), U9.6 (CANL)
CAN_RX: U1.45 (PB8), U9.3 (RXD)
CAN_TX: U1.46 (PB9), U9.2 (TXD)
CS_FL: U1.25 (PB12), U3.1 (~CS)
CURR_SENSE: TP5.1, U1.19 (PB1), U7.7 (VOUT)
DB_LED: R7.2, U1.38 (PA15)
EXTINT_GPS: J1.3, U1.40 (PB4)
GND: C1.2, C2.2, C3.2, C4.2, C5.2, C6.2, C7.2, C8.1, C9.1, C10.2, C11.2, C12.2, C13.2, C14.2, C15.2, C16.2, C17.2, C18.2, C20.2, C28.2, C29.2, D4.1 (K), D5.3 (VSS), D8.1 (K), D9.3 (VSS), J1.1, J2.1 (GND), J4.A3 (GND_A), J4.A6 (GND_A), J4.B4 (GND_A), J4.B5 (GND_A), J4.B6 (GND_A), J6.A1 (GND), J6.A12 (GND), J6.B1 (GND), J6.B12 (GND), Q1.2 (S), R11.1, R14.2, R15.2, R19.1, R20.1, SW1.1, TP6.1, U1.8 (VSSA), U1.23 (VSS), U1.35 (VSS), U1.47 (VSS), U3.4 (GND), U4.2 (GND), U4.5 (ST), U5.2 (GND), U5.5 (ST), U6.2 (GND), U6.5 (ST), U7.5 (GND), U9.4 (GND1), U9.5 (GND2), U10.1 (GND), Y1.2, Y1.4
MISO_FL: U1.27 (PB14), U3.2 (DO(IO1))
MOSI_FL: U1.28 (PB15), U3.5 (DI(IO0))
unnamed: BZ1.2 (+), Q1.3 (D), R12.1
unnamed: BZ1.1 (-), D10.1 (K), D11.1 (K), R12.2
unnamed: D4.2 (A), R4.1
unnamed: D5.2 (DOUT), D9.4 (DIN)
unnamed: D8.2 (A), R7.1
unnamed: J6.A5 (CC1), R14.1
unnamed: J6.B5 (CC2), R15.1
unnamed: Q1.1 (G), R9.1
unnamed: TP11.1, U1.10 (PA0)
unnamed: TP10.1, U1.11 (PA1)
unnamed: TP9.1, U1.12 (PA2)
unnamed: R13.1, U3.3 (IO2)
OSC_IN: C3.1, U1.5 (PD0), Y1.1
OSC_OUT: C20.1, U1.6 (PD1), Y1.3
RESET_FL: R3.1, U1.29 (PA8), U3.7 (IO3)
RGB_DATA: D5.4 (DIN), U1.39 (PB3)
RST_GPS: J1.4, U1.41 (PB5)
SCK_FL: U1.26 (PB13), U3.6 (CLK)
SCL_GPS: J1.6, R6.2, U1.42 (PB6)
SDA_GPS: J1.5, R5.1, U1.43 (PB7)
STM_RESET: C7.1, R2.1, SW1.2, U1.7 (NRST)
SWCLK: J2.4 (SWCLK), U1.37 (PA14)
SWDIO: J2.3 (SWDIO), U1.34 (PA13)
USB_D+: J6.A6 (D+), J6.B6 (D+), R8.2, U1.33 (PA12)
USB_D-: J6.A7 (D-), J6.B7 (D-), U1.32 (PA11)
V_MUX: C5.1, C6.1, TP4.1, U4.3 (*CE), U4.6 (VOUT), U5.3 (*CE), U5.6 (VOUT), U6.3 (*CE), U6.6 (VOUT), U7.1 (IP+), U7.2 (IP+), U7.8 (VCC)
V_PSU: C1.1, J4.A1 (3.3V_A), J4.A2 (3.3V_A), TP1.1, U4.1 (VIN)
V_REGUSB: C2.1, C29.1, TP2.1, U5.1 (VIN), U10.2 (VO)
V_SWD: C4.1, J2.2 (3V3), TP3.1, U6.1 (VIN)

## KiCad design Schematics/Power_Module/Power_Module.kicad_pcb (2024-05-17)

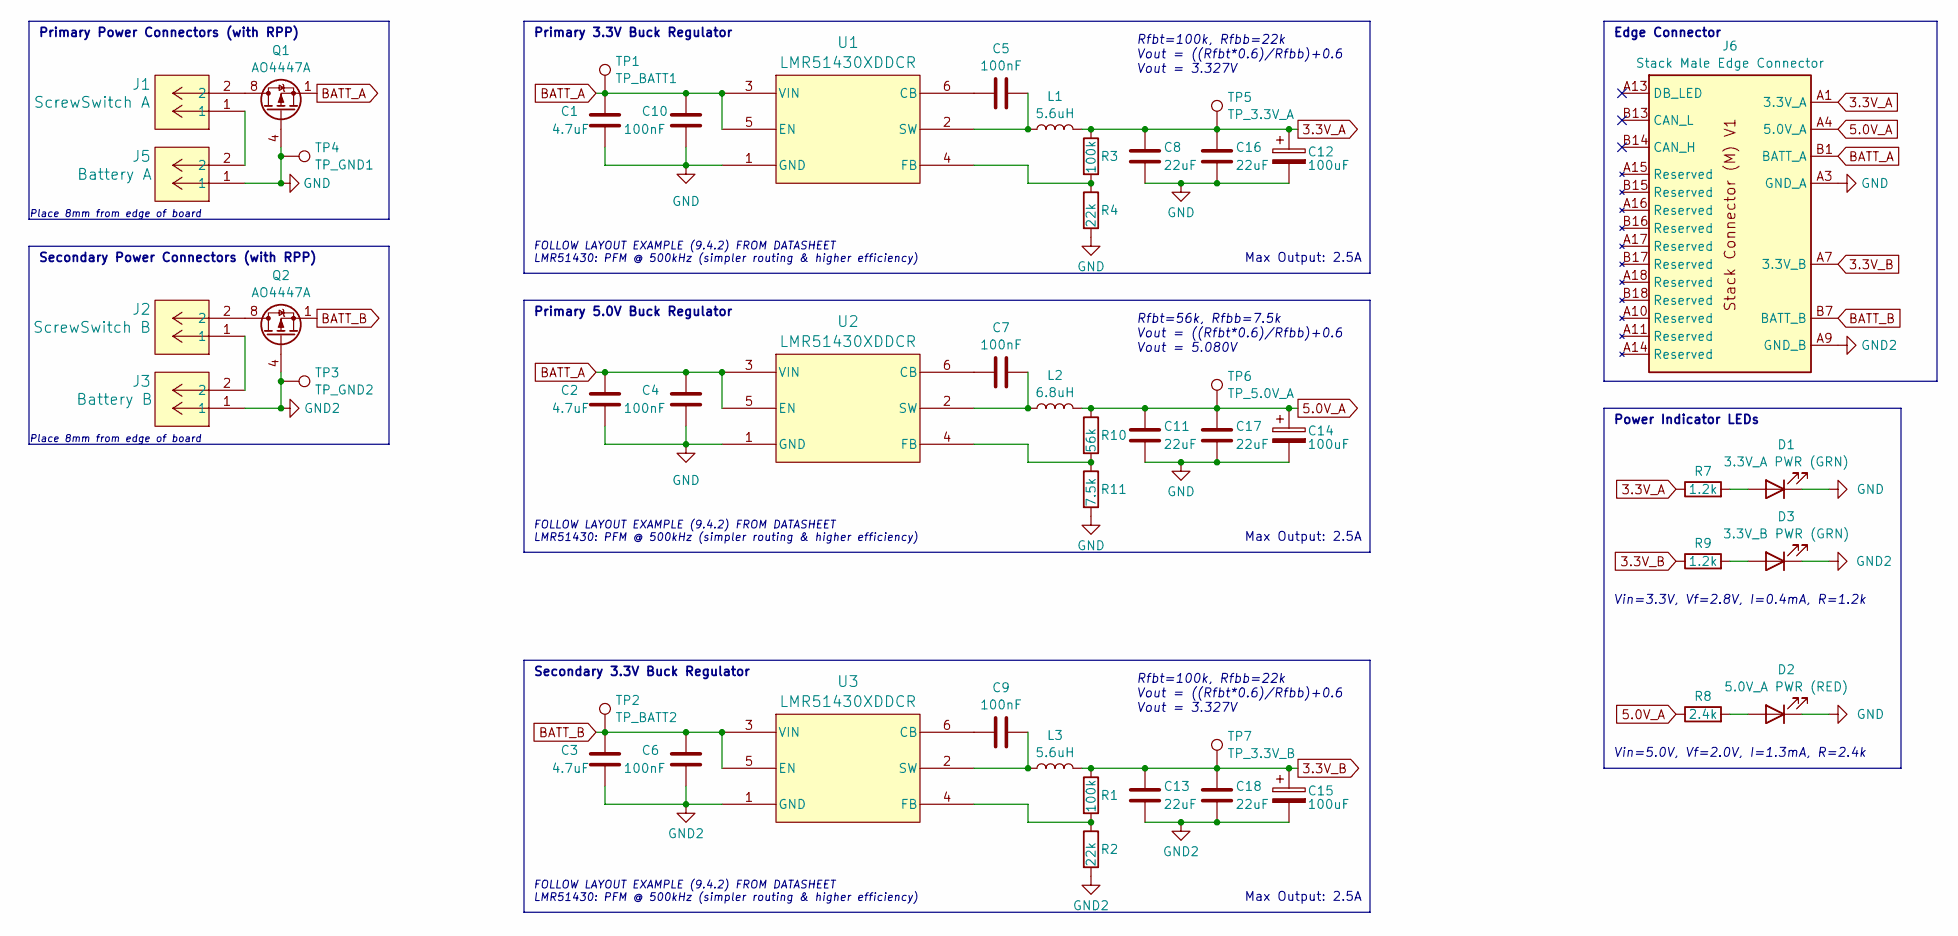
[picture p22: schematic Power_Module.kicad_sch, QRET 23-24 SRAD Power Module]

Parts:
C1, C2, C3: 4.7uF; C_0805_2012Metric; LCSC C1779
C4, C5, C6, C7, C9, C10: 100nF; C_0603_1608Metric; LCSC C14663
C8, C11, C13, C16, C17, C18: 22uF; C_0805_2012Metric; LCSC C45783
C12, C14, C15: 100uF; CP_Elec_6.3x5.9; Digikey 732-8419-1-ND
D1: 3.3V_A PWR (GRN); LED_0805_2012Metric; LCSC C2297
D2: 5.0V_A PWR (RED); LED_0805_2012Metric; LCSC C84256
D3: 3.3V_B PWR (GRN); LED_0805_2012Metric; LCSC C2297
J1: ScrewSwitch A; CONN_2-1445057-2_TYCO; Digikey A33212CT-ND
J2: ScrewSwitch B; CONN_2-1445057-2_TYCO; Digikey A33212CT-ND
J3: Battery B; CONN_2-1445057-2_TYCO; Digikey A33212CT-ND
J5: Battery A; CONN_2-1445057-2_TYCO; Digikey A33212CT-ND
J6: Stack Male Edge Connector; BUS_PCIexpress_x1
L1, L3: 5.6uH; L_Bourns_SRN8040TA; Digikey SDCHA1V8040-5R6-R
L2: 6.8uH; L_Bourns_SRN8040TA; Digikey HPC 8040NC-6R8M
Q1, Q2: AO4447A; SOIC-8_3.9x4.9mm_P1.27mm; LCSC C125867
R1, R3: 100k; R_0603_1608Metric; LCSC C25803
R2, R4: 22k; R_0603_1608Metric; LCSC C31850
R7, R9: 1.2k; R_0603_1608Metric; LCSC C22765
R8: 2.4k; R_0603_1608Metric; LCSC C22940
R10: 56k; R_0603_1608Metric; LCSC C23206
R11: 7.5k; R_0603_1608Metric; LCSC C23234
TP1: TP_BATT1; TestPoint_Pad_2.0x2.0mm
TP2: TP_BATT2; TestPoint_Pad_2.0x2.0mm
TP3: TP_GND2; TestPoint_Pad_2.0x2.0mm
TP4: TP_GND1; TestPoint_Pad_2.0x2.0mm
TP5: TP_3.3V_A; TestPoint_Pad_2.0x2.0mm
TP6: TP_5.0V_A; TestPoint_Pad_2.0x2.0mm
TP7: TP_3.3V_B; TestPoint_Pad_2.0x2.0mm
U1, U2, U3: LMR51430XDDCR; SOT-23-6_Handsoldering; Digikey 296-LMR51430XDDCRCT-ND

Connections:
3.3V_A: C8.1, C12.1, C16.1, J6.A1 (3.3V_A), J6.A2 (3.3V_A), L1.2, R3.1, R7.1, TP5.1
3.3V_B: C13.1, C15.1, C18.1, J6.A7 (3.3V_B), J6.A8 (3.3V_B), L3.2, R1.1, R9.1, TP7.1
5.0V_A: C11.1, C14.1, C17.1, J6.A4 (5.0V_A), J6.A5 (5.0V_A), L2.2, R8.1, R10.1, TP6.1
BATT_A: C1.1, C2.1, C4.1, C10.1, J6.B1 (BATT_A), J6.B2 (BATT_A), J6.B3 (BATT_A), Q1.1 (S), Q1.2 (S), Q1.3 (S), TP1.1, U1.3 (VIN), U1.5 (EN), U2.3 (VIN), U2.5 (EN)
BATT_B: C3.1, C6.1, J6.B7 (BATT_B), J6.B8 (BATT_B), J6.B9 (BATT_B), Q2.1 (S), Q2.2 (S), Q2.3 (S), TP2.1, U3.3 (VIN), U3.5 (EN)
GND: C1.2, C2.2, C4.2, C8.2, C10.2, C11.2, C12.2, C14.2, C16.2, C17.2, D1.1 (K), D2.1 (K), J5.1, J6.A3 (GND_A), J6.A6 (GND_A), J6.B4 (GND_A), J6.B5 (GND_A), J6.B6 (GND_A), Q1.4 (G), R4.2, R11.2, TP4.1, U1.1 (GND), U2.1 (GND)
GND2: C3.2, C6.2, C13.2, C15.2, C18.2, D3.1 (K), J3.1, J6.A9 (GND_B), J6.A12 (GND_B), J6.B10 (GND_B), J6.B11 (GND_B), J6.B12 (GND_B), Q2.4 (G), R2.2, TP3.1, U3.1 (GND)
unnamed: D1.2 (A), R7.2
unnamed: D2.2 (A), R8.2
unnamed: D3.2 (A), R9.2
unnamed: J1.1, J5.2
unnamed: J1.2, Q1.5 (D), Q1.6 (D), Q1.7 (D), Q1.8 (D)
unnamed: J2.1, J3.2
unnamed: J2.2, Q2.5 (D), Q2.6 (D), Q2.7 (D), Q2.8 (D)
unnamed: C5.2, U1.6 (CB)
unnamed: R3.2, R4.1, U1.4 (FB)
unnamed: C5.1, L1.1, U1.2 (SW)
unnamed: C7.2, U2.6 (CB)
unnamed: R10.2, R11.1, U2.4 (FB)
unnamed: C7.1, L2.1, U2.2 (SW)
unnamed: C9.2, U3.6 (CB)
unnamed: R1.2, R2.1, U3.4 (FB)
unnamed: C9.1, L3.1, U3.2 (SW)

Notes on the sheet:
Place 8mm from edge of board
Max Output: 2.5A
Primary Power Connectors (with RPP)
Primary 5.0V Buck Regulator
Primary 3.3V Buck Regulator
Secondary Power Connectors (with RPP)
FOLLOW LAYOUT EXAMPLE (9.4.2) FROM DATASHEET LMR51430: PFM @ 500kHz (simpler routing & higher efficiency)
Rfbt=56k, Rfbb=7.5k Vout = ((Rfbt*0.6)/Rfbb)+0.6 Vout = 5.080V
Power Indicator LEDs
Vin=5.0V, Vf=2.0V, I=1.3mA, R=2.4k
Vin=3.3V, Vf=2.8V, I=0.4mA, R=1.2k
Rfbt=100k, Rfbb=22k Vout = ((Rfbt*0.6)/Rfbb)+0.6 Vout = 3.327V
Edge Connector
Secondary 3.3V Buck Regulator

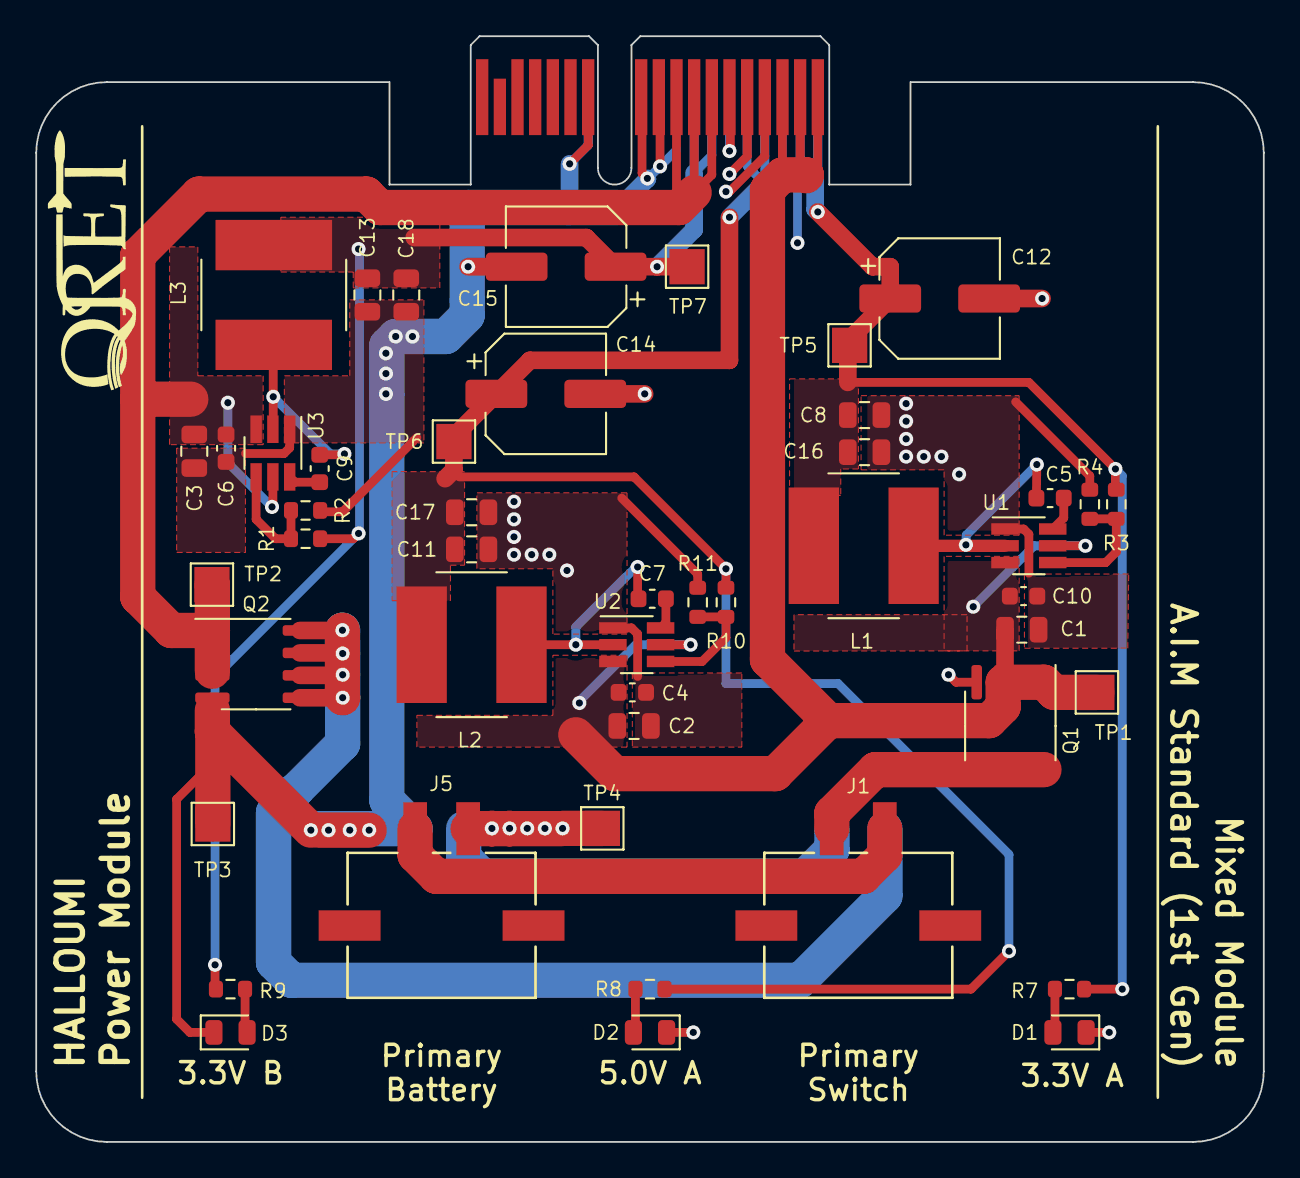
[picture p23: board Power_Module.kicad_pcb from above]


Board: 4 copper layers, 69.5 x 62.6 mm, 50 parts (2 on the bottom side), 23 nets.

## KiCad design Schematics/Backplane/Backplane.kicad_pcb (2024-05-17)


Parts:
H1, H2, H3, H4: MountingHole; MountingHole_3.2mm_M3_ISO14580_Pad
J1: Edge Connector (SLOT 1); AMPHENOL_10018784-10210TLF; Digikey 609-2029-ND
J2: Edge Connector (SLOT 2); AMPHENOL_10018784-10210TLF; Digikey 609-2029-ND
J3: Edge Connector (SLOT 3); AMPHENOL_10018784-10210TLF; Digikey 609-2029-ND
J4: Edge Connector (SLOT 4); AMPHENOL_10018784-10210TLF; Digikey 609-2029-ND
J5: Edge Connector (SLOT 5); AMPHENOL_10018784-10210TLF; Digikey 609-2029-ND
R1, R2: 120R; R_0805_2012Metric_Pad1.20x1.40mm_HandSolder; Digikey A129738CT-ND

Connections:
3.3V_A: J1.A1 (3.3V_A), J1.A2 (3.3V_A), J2.A1 (3.3V_A), J2.A2 (3.3V_A), J3.A1 (3.3V_A), J3.A2 (3.3V_A), J4.A1 (3.3V_A), J4.A2 (3.3V_A), J5.A1 (3.3V_A), J5.A2 (3.3V_A)
3.3V_B: J1.A7 (3.3V_B), J1.A8 (3.3V_B), J2.A7 (3.3V_B), J2.A8 (3.3V_B), J3.A7 (3.3V_B), J3.A8 (3.3V_B), J4.A7 (3.3V_B), J4.A8 (3.3V_B), J5.A7 (3.3V_B), J5.A8 (3.3V_B)
5.0V_A: J1.A4 (5.0V_A), J1.A5 (5.0V_A), J2.A4 (5.0V_A), J2.A5 (5.0V_A), J3.A4 (5.0V_A), J3.A5 (5.0V_A), J4.A4 (5.0V_A), J4.A5 (5.0V_A), J5.A4 (5.0V_A), J5.A5 (5.0V_A)
BATT_A: J1.B1 (BATT_A), J1.B2 (BATT_A), J1.B3 (BATT_A), J2.B1 (BATT_A), J2.B2 (BATT_A), J2.B3 (BATT_A), J3.B1 (BATT_A), J3.B2 (BATT_A), J3.B3 (BATT_A), J4.B1 (BATT_A), J4.B2 (BATT_A), J4.B3 (BATT_A), J5.B1 (BATT_A), J5.B2 (BATT_A), J5.B3 (BATT_A)
BATT_B: J1.B7 (BATT_B), J1.B8 (BATT_B), J1.B9 (BATT_B), J2.B7 (BATT_B), J2.B8 (BATT_B), J2.B9 (BATT_B), J3.B7 (BATT_B), J3.B8 (BATT_B), J3.B9 (BATT_B), J4.B7 (BATT_B), J4.B8 (BATT_B), J4.B9 (BATT_B), J5.B7 (BATT_B), J5.B8 (BATT_B), J5.B9 (BATT_B)
CAN_H: J1.B14 (CAN_H), J2.B14 (CAN_H), J3.B14 (CAN_H), J4.B14 (CAN_H), J5.B14 (CAN_H), R1.1, R2.1
CAN_L: J1.B13 (CAN_L), J2.B13 (CAN_L), J3.B13 (CAN_L), J4.B13 (CAN_L), J5.B13 (CAN_L), R1.2, R2.2
GND1: J1.A3 (GND_A), J1.A6 (GND_A), J1.B4 (GND_A), J1.B5 (GND_A), J1.B6 (GND_A), J2.A3 (GND_A), J2.A6 (GND_A), J2.B4 (GND_A), J2.B5 (GND_A), J2.B6 (GND_A), J3.A3 (GND_A), J3.A6 (GND_A), J3.B4 (GND_A), J3.B5 (GND_A), J3.B6 (GND_A), J4.A3 (GND_A), J4.A6 (GND_A), J4.B4 (GND_A), J4.B5 (GND_A), J4.B6 (GND_A), J5.A3 (GND_A), J5.A6 (GND_A), J5.B4 (GND_A), J5.B5 (GND_A), J5.B6 (GND_A)
GND2: J1.A9 (GND_B), J1.A12 (GND_B), J1.B10 (GND_B), J1.B11 (GND_B), J1.B12 (GND_B), J2.A9 (GND_B), J2.A12 (GND_B), J2.B10 (GND_B), J2.B11 (GND_B), J2.B12 (GND_B), J3.A9 (GND_B), J3.A12 (GND_B), J3.B10 (GND_B), J3.B11 (GND_B), J3.B12 (GND_B), J4.A9 (GND_B), J4.A12 (GND_B), J4.B10 (GND_B), J4.B11 (GND_B), J4.B12 (GND_B), J5.A9 (GND_B), J5.A12 (GND_B), J5.B10 (GND_B), J5.B11 (GND_B), J5.B12 (GND_B)

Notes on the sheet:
CANBUS Termination
Place resistors at either end of CANBUS traces
Mounting Holes
Edge Connectors
Place on back of PCB

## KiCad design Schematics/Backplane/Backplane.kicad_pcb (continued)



Board: 2 copper layers, 69.5 x 99.0 mm, 15 parts (2 on the bottom side), 9 nets.

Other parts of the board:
H5, H6, H7, H8: MountingHole; MountingHole_3.2mm_M3_ISO14580_Pad

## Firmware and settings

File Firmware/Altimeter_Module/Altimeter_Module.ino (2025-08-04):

/*
Authors: Brent Naumann, Tristan Alderson, Kennan Bays, Caelan Donovan, Ethan Toste
Env: Arduino 1.8.10, STM32duino 2.7.1
Updated: Aug.04.2025
Purpose: QRET SRAD Avionics module - AIM Altimeter Module Firmware V 2.0 (STINGER)

Sensors used:
 - ms5611 : Pressure and Temperature
 - mpu6050 : Gyroscope
 - kx134 : accelerometer (SIKE)
*/

//Libraries to include
#include <Wire.h>
#include <SimpleKalmanFilter.h>
#include <Adafruit_MPU6050.h>
#include <SparkFun_KX13X.h> 
#include <SerialFlash.h>
#include <SPI.h>
#include "flashTable.h"
#include <tone.h>
#include <CANpackets.h>
#include "STM32_CAN.h" //IMPORTANT: DO NOT DOWNLOAD THE LATEST VERSION (DOWNLOAD 1.1.2)
#include "pinouts.h"
#include <HardwareSerial.h>
#include "MS5611.h" // https://github.com/RobTillaart/MS5611


// TODO: RE-WORK BUZZER FOR ALL MODULES
#define BUZZER_TONE 1000
#define BUZZER_TONE_Q 500
const uint32_t BEEP_FREQ = 1000;

#define SERIAL_BAUD_RATE 115200
//#define SERIAL_BAUD_RATE 9600

//--- FILTER SETTINGS
#define M_UNCERT    15        //Uncertainty of taken measurements (varience)
#define EST_UNCERT  M_UNCERT  //Uncertainty of Kalman estimation (changes over time)
#define NOISE_SENS  0.008    //The filters sensitivity to unexpected changes. Range: 0.001 ->1
#define LAPSE_RATE -0.0065   //[K/m] change in temperature over height


//--- FLASH SETTINGS
uint16_t flashDelay = 250; // How frequently the debug LED should be toggled
uint32_t lastFlash = 0; // Last millis() the debug LED was toggle at

const uint8_t TABLE_NAME = 0;
const uint8_t TABLE_COLS = 8;
const uint32_t TABLE_SIZE = 16646144;
// IMPORTANT!!!; AT LEAST 2 BLOCK OF SPACE MUST BE RESERVED FOR FILE SYSTEM
// 16MiB = 16777216B, 2x 64KiB blocks = 131072B
// 16MiB - 128KiB = 16646144B

//--- CANBUS DATA SETTINGS
#define CANBUS_DATAINT 500 //[ms] interval bewteen each CANBUS message send.

//--- PREFLIGHT SETTINGS
#define PRE_DATAINT 35  //[ms] interval bewteen each log to FLASH.

//--- LAUNCH SETTINGS
#define LAUNCH_THRESHOLD  25  // [m/s]-mpu ; [g]-qma. Acceleration threshold to declare launch
#define LAUNCH_GRACE      75 // [ms] Time for measurements to be above threshold before Launch declared

//--- ASCENT SETTINGS
#define ASC_DATAINT 20 //  [ms] interval bewteen each log to FLASH.
#define APO_GRACE   500 // [ms] Time for measurements to be above threshold before Apogee is declared

//--- DESCENT SETTINGS
#define DROGUE_DATAINT 20 //  [ms] interval between each log to FLASH.
#define MAIN_DATAINTFAST 500 // [ms] interval between each log to FLASH - slowed rate before 5000 ms
#define MAIN_DATAINTSLOW 1000 // [ms] interval between each log to FLASH - slowed rate after 5000 ms
#define LAND_THRESHOLD -0.3//[m/s] Velocity Threshold to declare land
#define LAND_GRACE  2000 // [ms] Time for measurements to be above threshold before Landing is declared
const uint16_t MAIN_DEPLOY_THRESHOLD = 1500/3.281;

//--- LAND SETTINGS
#define LAND_DATAINT 1000  //[ms] interval between each log to FLASH.
#define LAND_SLOW_DATAINT 2000 //[ms] interval between each log to FLASH.



// Global objects to declare
HardwareSerial usb(USB_RX_PIN, USB_TX_PIN);
//#define usb Serial              //For debugging when not using CANBUS

SimpleKalmanFilter kalmanFilter(M_UNCERT,EST_UNCERT,NOISE_SENS); 
MS5611 ms5611(MS5611_ADDR, &Wire);


Adafruit_MPU6050 mpu6050;
SparkFun_KX134 kxAccel;

FlashTable flash = FlashTable(TABLE_COLS, 16384, TABLE_SIZE, TABLE_NAME, 128);

STM32_CAN canb( CAN1, ALT );    //CAN1 ALT is PB8+PB9
static CAN_message_t CAN_TX_msg ;

//--- Global Variables
//sensors

outputData kxData;          //For kx134
sensors_event_t a, g, temp;  // for mpu6050

float Po;
float To;

//state machine
uint8_t STATE = 0;  //State flag for state machine


//Pre-Launch
unsigned long potentialLaunchStart; //saves time of possible launch start
bool potentialLaunch = 0;

//Ascent

unsigned long potentialApoStart;
bool potentialApo = 0;

//decent
unsigned long potentialLandStart;
bool potentialLand = 0;

//ascent-decent shared
float vel;  //Decent velocity
float prev_alt;  //velocity from previous measurement
unsigned long curTime;
unsigned long prevTime;

//data logging and CANBUS
unsigned long lastLog; // Time of last data log
unsigned long lastSend; // Time of last CANBUS send

//extra timers
int mainTimer = 0;
int landingTimer =0;

// ---   ---   ---   ---   ---   ---   ---   ---   ---   ---   ---   ---   ---   ---   ---   ---   ---   ---   ---

//      SETUP

// ---   ---   ---   ---   ---   ---   ---   ---   ---   ---   ---   ---   ---   ---   ---   ---   ---   ---   ---

void setup(){

  // Configure pinmodes
  pinMode(BUZZER_A_PIN, OUTPUT);
  pinMode(BUZZER_B_PIN, OUTPUT);
  pinMode(STATUS_LED_PIN, OUTPUT);
  pinMode(FIRE_MAIN_PIN,OUTPUT);
  pinMode(FIRE_DROGUE_PIN,OUTPUT);
  

  // Configure SPI
  SPI.setSCLK(PB13);
  SPI.setMISO(PB14);
  SPI.setMOSI(PB15);

  //Configure I2C PINS
  Wire.setSDA(SDA_PIN);
  Wire.setSCL(SCL_PIN);
  Wire.begin();

  //Start CANBUS
  canb.begin(); //automatic retransmission can be done using arg "true"
  canb.setBaudRate(500000); //500kbps

  //Start Serial
  usb.begin(SERIAL_BAUD_RATE);
  delay(1000);

  usb.print("BUZZER REACHED");      

  initBuzzer();
  setBuzzerFreq(BEEP_FREQ);

  // // STARTUP BEEP
  startBuzzer();
  delay(1000);
  stopBuzzer();
    
  digitalWrite(STATUS_LED_PIN,LOW);

//    for (int i=0 ; i<5 ; i++){
//      digitalWrite(STATUS_LED_PIN,HIGH);
//      delay(250);
//      digitalWrite(STATUS_LED_PIN,LOW);
//      delay(750);
//    }

  usb.println("Connecting to required devices...");
            
  /*------------------*\
  |    FLASH SETUP    |
  \*------------------*/
  usb.print("SEARCHING: SPI Flash chip");
  while (!SerialFlash.begin(FLASH_CS_PIN)) {
    delay(250);
    //toggleStatusLED();
  }//while
  usb.println("  - CONNECTED");
  
  while (SerialFlash.ready() == false) {}  
  // Initialize FlashTable object
  flash.init(&SerialFlash, &usb);
  // Note done loading
  for (int i=0; i<3; i++) {
    startBuzzer();
    delay(100);
    stopBuzzer();
    delay(100);
  }


  /*------------------*\
  |    MS5611 SETUP    |
  \*------------------*/
  usb.print("SEARCHING: MS5611");      
  while (!ms5611.begin()) {
    delay(10);
  }
  usb.println("  - CONNECTED"); //MS5611 connected

  // Set oversampling
  ms5611.setOversampling(OSR_ULTRA_LOW);

  /*-------------------*\
  |    MPU6050 SETUP    |
  \*-------------------*/  
    usb.print("SEARCHING: MPU6050");

    while(!mpu6050.begin(MPU6050_ADDR)) {
      delay(10);
    }//while()
    usb.println("  - CONNECTED");    //ms6050 connected

    mpu6050.setAccelerometerRange(MPU6050_RANGE_16_G); 
    mpu6050.setGyroRange(MPU6050_RANGE_500_DEG);
    mpu6050.setFilterBandwidth(MPU6050_BAND_21_HZ);



  /*--------------------*\
  |    KX134 SETUP    |
  \*--------------------*/
  //float qmaOffsetX = -1.495;
  //float qmaOffsetY = -0.485;
  //float qmaOffsetZ = 0.825;

  // usb.print("SEARCHING: KX134");

  // while(!kxAccel.begin(KX134_ADDR)) {       // Wait for kx134 to connect
  //     delay(10);  
  //     for (byte address = 1; address < 127; ++address) {
  //       Wire.beginTransmission(address);
  //       byte error = Wire.endTransmission();

  //       if (error == 0) {
  //         Serial.print("Found device at 0x");
  //         Serial.println(address, HEX);
  //       }
  //     }
  // }
  // usb.println("  - CONNECTED");

  // usb.println("Resetting KX134...");
  // kxAccel.softwareReset();
  // delay(100); // Wait for reset to complete

  // usb.println("Setting range...");
  // kxAccel.setRange(SFE_KX134_RANGE32G);
  // usb.println("KX134 configured.");

  // Get base measurements
  usb.println("Aquiring base Pressure...");
  Po = altimeterBasePres(500);
  usb.print("Base Pressure: ");
  usb.println(Po);
  
  usb.println("Aquiring base Temperature...");
  To = altimeterBaseTemp(500);
  usb.print("Base Temperature: ");
  usb.println(To);   
  
  usb.println("");
  usb.println("All sensors set up and configured.");
  usb.println("");

  // Startup delay - Check to enter debug mode
  usb.println("[MDE] SEND SERIAL TO ENTER DEBUG");
  uint32_t startTime = millis();
  while (!usb.available() and millis()-startTime < 4000) {}
  
  if (usb.available()) {
    byte d = usb.read();
    emptySerialBuffer();
    usb.println("[MDE] Entered Debug Mode");
    debugMode();
    while (true) {}
  }//if

  usb.println("Beginning PreFlight...");

  // kxAccel.enableAccel();  //Start accelerometer reading

  digitalWrite(STATUS_LED_PIN, HIGH);

}//setup()

// ---   ---   ---   ---   ---   ---   ---   ---   ---   ---   ---   ---   ---   ---   ---   ---   ---   ---   ---

//      LOOP

// ---   ---   ---   ---   ---   ---   ---   ---   ---   ---   ---   ---   ---   ---   ---   ---   ---   ---   ---

void loop(){

  /*---------|----------*\
      |SENSOR READING|    
  \*---------|----------*/
  
  //read pressure/temp
  ms5611.read();     //Read the data from the ms5611, which gets stored in object

  //Get variables for pressure and temperature
  float P = ms5611.getPressurePascal();  // Pascals
  float T = ms5611.getTemperature(); // Celcius

  //Kalman Filtering on pressure
  float P_filter = kalmanFilter.updateEstimate(P);

  //Find Altitude from filtered Pressure
  float alt = altitudeFind(P_filter,Po,To);

  // TODO: FIX IN THE FUTURE
  // Override the inaccurate altitude system using raw pressure reading (im assuming its in pascals)
  alt = (288.15d/0.0065d) * (1-pow(P_filter/101325.0f, 0.190284f));

  //read gyro
  mpu6050.getEvent(&a, &g, &temp);

  //read accelerometer
  //kxAccel.getAccelData(&kxData);
  //kxAccel.offsetValues(kxData.xData, kxData.yData, kxData.zData);

  //--- CANBUS DATA SENDING
  if (millis() - lastSend >= CANBUS_DATAINT){
    //send Temperature, altitude, and Flight stage
    //sendCANtemp(T);
    usb.print("Pres(Pa): ");
    usb.print(P_filter, 2);
    usb.print(", Temp(C): ");
    usb.print(T);
    usb.print(", Alt(m): ");
    usb.println(alt);
    sendCANaltitude(alt);
    sendCANstage(STATE);
    lastSend = millis();
  }//if

  /*---\/---\/---\/---\/---*\
       |  STATE MACHINE |    
  \*---/\---/\---/\---/\---*/

  switch (STATE){
    case 0:   //Pre-Flight Stage  
      // Data logging
      if( millis() - lastLog >= PRE_DATAINT){
        logDataToFlash(P,P_filter,T,&a,&g);
        lastLog = millis();
      }//if
      //Perform Launch Checks
      if(detectLaunch()){
          STATE = 1;  
          digitalWrite(STATUS_LED_PIN,LOW);
      }//if
      break;
      
    case 1:   //Ascending
      //logging data 
      if( millis() - lastLog >= ASC_DATAINT){
        logDataToFlash(P,P_filter,T,&a,&g);
        lastLog = millis();
      }//if
       
      //Perform Apogee check
      if(detectApogee(alt)){
        STATE = 3;
        digitalWrite(FIRE_DROGUE_PIN,HIGH);
        usb.println(F("FIRING DROGUE"));
      }//if
      
      //updating prevs
      prevTime = curTime;
      prev_alt = alt;
      break;

    case 3:   //Descending with drogue
      //logging data
      if( millis() - lastLog >= DROGUE_DATAINT){
        logDataToFlash(P,P_filter,T,&a,&g);
        lastLog = millis();
      }//if

      //fire main parachute if necessary
      if(alt<= MAIN_DEPLOY_THRESHOLD){
        digitalWrite(FIRE_MAIN_PIN, HIGH);
        usb.println(F("FIRING MAIN"));
        STATE = 4;
        mainTimer = millis();
      }//if
      break;
      
    case 4:   //descending with main
      //logging data
      if(millis() - mainTimer <= 5000){
        if(millis() - lastLog >= MAIN_DATAINTFAST){
          logDataToFlash(P,P_filter,T,&a,&g);
          lastLog = millis();
        }//if
      }//if
      else if(millis() - mainTimer > 5000){
        if(millis() - lastLog >= MAIN_DATAINTSLOW){
          logDataToFlash(P,P_filter,T,&a,&g);
          lastLog = millis();
        }//if
      }//if
      
      //perform Landing check
      if(detectLand(alt)){
        landingTimer = millis();
        STATE = 5;
        usb.println("LANDED");
      }//if
      //updating prevs
      prevTime = curTime;
      prev_alt = alt;
      break;
      
    case 5:   // Landed
      //logging data
      if (millis() - landingTimer <= 1800000){
        if( millis() - lastLog >= LAND_DATAINT){
          logDataToFlash(P,P_filter,T,&a,&g);
          lastLog = millis();

        }//if
      }
      //slower logging rate after 30 mins to save power
      else if (millis() - landingTimer > 1800000 && millis() - landingTimer < 3600000){
        if( millis() - lastLog >= LAND_SLOW_DATAINT){
          logDataToFlash(P,P_filter,T,&a,&g);
          lastLog = millis();

        }//if
      }
      //power save mode after 60 mins
      else if (millis() - landingTimer > 36000000){
        
      }
      break;

  }//switch
}//loop()

/*---\/---\/---\/---\/---*\
     |  DATA LOGGING |    
\*---/\---/\---/\---/\---*/

void logDataToFlash( float pressure, float pressure_filter, float temp,sensors_event_t *a, sensors_event_t *g){
  uint32_t dataArr[8] = {0,0,0,0,0,0,0,0};

  dataArr[0] = millis();
  dataArr[1] = uint32_t(pressure);
  dataArr[2] = uint32_t(temp*1000);
  // accelleration data (from mpu or qma)
  // dataArr[4] = static_cast<uint32_t>(a->acceleration.x*1e6);
  // dataArr[5] = static_cast<uint32_t>(a->acceleration.y*1e6);
  dataArr[3] = flash.unsignify(a->acceleration.z*10000);
  
  //gyro data
  dataArr[4] = flash.unsignify(g->gyro.x*10000);
  dataArr[5] = flash.unsignify(g->gyro.y*10000);
  dataArr[6] = flash.unsignify(g->gyro.z*10000);

  // dataArr[7] = flash.unsignify(altitudeFind(pressure_filter, altimeterBasePres(500),altimeterBaseTemp(500)));

  //state
  dataArr[7] = STATE;

  //write to FLASH
  bool success = flash.writeRow(dataArr);
  if (success) {
    //usb.println("[MDE] Data logged successfully");
  } else {
      usb.println("[MDE] Flash write failed!");
  }

}//logDataToFlash()

/*---\/---\/---\/---\/---*\
     |  EVENT CHECKS |    
\*---/\---/\---/\---/\---*/
bool detectLaunch(){
  if (a.acceleration.z > LAUNCH_THRESHOLD){ //check if sensor reading is higher than 
    
    if (!potentialLaunch) {
      //if first measurement, begin launch countdown
      potentialLaunch = 1;
      potentialLaunchStart = millis();
    } else {
      //if not first, check time since first
      if (millis() - potentialLaunchStart >= LAUNCH_GRACE){
        //THEN LAUNCH IS ON
        return true;
      }//if
    }//if
    
  } else {
    potentialLaunch = 0;
  }//if
  return false;
}//end detectLaunch


bool detectApogee(float alt){
  curTime = millis();
  float dh = (alt - prev_alt)/(curTime-prevTime) * 1000;

  vel = 0.9*vel + 0.1*dh;
   
  if (vel < -0.1) {    //check if velocity is negative (with some error margin)
    if (!potentialApo) {
      //if first measurement, begin apogee countdown
      potentialApo = 1;
      potentialApoStart = millis();
    } else {
      //if not first, check time since first
      if (millis() - potentialApoStart >= APO_GRACE){
        //THEN WE HAVE HIT APOGEE
        return true;
      }//if
    }//if
    
  } else {
    potentialApo = 0;    
  }//if
  
  return false;    
}//detectApogee()

bool detectLand(float alt) {
  curTime = millis() ;
  float dh = (alt - prev_alt)/(curTime-prevTime) *1000;
  
  vel = 0.9*vel + 0.1*dh;
  
  if (vel > LAND_THRESHOLD && vel <= LAND_THRESHOLD) {  //check if velocity is less than -0.5 [m/s]
    
    if (!potentialLand) {
      //if first measurement, begin Land countdown
      potentialLand = 1;
      potentialLandStart = millis();
      
    } else {
      //if not first, check time since first
      if (millis() - potentialLandStart >= LAND_GRACE){
        //THEN WE HAVE LANDED
        return true;      
      }//if
    }//if
  
  } else {
    potentialLand = 0;
  }//if

  return false;  
}//detectLand()

/*---\/---\/---\/---\/---*\
      |  DEBUG MENU |    
\*---/\---/\---/\---/\---*/

/*
 * Empties all bytes from incoming Serial buffer.
 * Used by Debug mode
 */
void emptySerialBuffer() {
  while (usb.available()) {usb.read();}
}//emptySerialBuffer()

/*
 * Called when Debug mode is activated;
 * all normal board functions will cease.
 * Only purpose is to respond to serial
 * commands.
 */
void debugMode() {

  // Status LED static "ON"
  digitalWrite(STATUS_LED_PIN, HIGH);

  while (true) {

    // Empty buffer
    emptySerialBuffer();

    // Wait for command
    while (!usb.available()) {}
    uint8_t cmd = usb.read();

    if (cmd == 'I') {
      // "Identify" command; return board name
      usb.println(F("[MDE] STINGER_ALT"));
    }//if
    if (cmd == 'F') {
      // "FlashInfo" command; return flash usage stats
      usb.print(F("[MDE] "));
      usb.print(flash.getMaxSize());
      usb.print(F(","));
      usb.println(flash.getCurSize());   
    }//if
    if (cmd == 'D') {
      // "DumpFlash" command; dump all flash contents via serial
      flash.beginDataDump(&usb);
    }//if
    if (cmd == 'L') {
      // LOG DATA
      //Get variables for pressure and temperature
      float P = ms5611.getPressurePascal(); //pascals
      float T = ms5611.getTemperature(); //celcius
      float P_filter = kalmanFilter.updateEstimate(P);
      mpu6050.getEvent(&a, &g, &temp);
      logDataToFlash(P,P_filter,T,&a,&g);
    }  
    if (cmd == 'E') {
      // "EraseFlash" command; completely erase contents of flash.
      // Should be restarted afterwards
      usb.println(F("[MDE] Erasing Flash"));
      SerialFlash.eraseAll();
      while (SerialFlash.ready() == false) {}
      //flash.init(&SerialFlash);
      usb.println(F("[MDE] Complete"));
    }//if
    if (cmd == 'Q') {
        // QUERY SENSORS
        // kxAccel.enableAccel();
          //Read pressure/temperature
        ms5611.read();
        usb.println("[MDE] --MS5611--");
        usb.print(F("[MDE] Temperature (1.00C): "));
        usb.println(ms5611.getTemperature());
        usb.print(F("[MDE] Pressure (Pa): "));
        usb.println(ms5611.getPressurePascal());

        //read gyro
      sensors_event_t a, g, temp;
      mpu6050.getEvent(&a, &g, &temp);
      usb.println("[MDE] --MPU6050--");
      usb.print("[MDE] X Rotation (rad/s): ");
      usb.println(g.gyro.x);
      usb.print("[MDE] Y Rotation (rad/s): ");
      usb.println(g.gyro.y);
      usb.print("[MDE] Z Rotation (rad/s): ");
      usb.println(g.gyro.z);
      
        //read accelerometer
      // outputData kxData;
      //kxAccel.getAccelData(&kxData);
      //kxAccel.offsetValues(kxData.xData, kxData.yData, kxData.zData);

      // usb.println("[MDE] --kxAccel--");
      // usb.print("[MDE] X Acceleration (g): ");
      // usb.println(kxData.xData);
      // usb.print("[MDE] Y Acceleration (g): ");
      // usb.println(kxData.yData);
      // usb.print("[MDE] Z Acceleration (g): ");
      // usb.println(kxData.zData);   
    }//if

  }//while

}//debugMode()

/*
 * Updates the status LED; should be run in loop() 
 */
void handleStatusFlash() {
  if (millis() - lastFlash > flashDelay) {
    lastFlash = millis();
    // toggle LED
    digitalWrite(STATUS_LED_PIN, !digitalRead(STATUS_LED_PIN));
  }//if
}//handleStatusFlash()

/*---\/---\/---\/---\/---*\
    | ALTIMETER FUNC |    
\*---/\---/\---/\---/\---*/
float altitudeFind(float P, float Po, float To){
  float alt = (To/LAPSE_RATE)*( pow(P/Po,0.19026627) - 1 );
  return alt;
}//altitudeFind()

/*
 * Finding Po and To
 */
float altimeterBaseTemp(int sample){
  float sum = 0;

  for (int i=0 ; i<sample ; i++){
    ms5611.read();
    float Ti = ms5611.getTemperature(); //celcius
    sum +=Ti;
  }//for
  float To = sum/sample;

  return To;
}//altimeterBaseTemp()

float altimeterBasePres(int sample){
  float sum = 0;
  
  for (int i=0 ; i<sample ; i++){
    ms5611.read();
    float Pi = ms5611.getPressurePascal(); //pascals
    sum +=Pi;
  }//for
  float Po = sum/sample;

  return Po;
}//altimeterBasePres()

/*---\/---\/---\/---\/---*\
    | CANBUS FUNCTIONS |    
\*---/\---/\---/\---/\---*/

/*
 * Sends current altitude over CANBUS
 */
void sendCANaltitude(float alt){

  //Adjust altitude into uin32_t 
  //pushes decimals to first 8 bits
  int32_t altint = (alt);
  
  //Start shifting bits (b0 = LSB)
  uint8_t b0 = altint & 0xFF;
  uint8_t b1 = altint>>8 & 0xFF;
  uint8_t b2 = altint>>16 & 0xFF;
  uint8_t b3 = altint>>24 & 0xFF;
  
  //Build the CANBUS message
  CAN_TX_msg.id = (ALTIMETER_MOD_CANID+ALTITUDE_CANID);
  CAN_TX_msg.len = 4;
  
  CAN_TX_msg.buf[0] = b0;
  CAN_TX_msg.buf[1] = b1 ;
  CAN_TX_msg.buf[2] = b2 ;
  CAN_TX_msg.buf[3] = b3 ;
  
  canb.write(CAN_TX_msg);     //send
}//sendCANaltitude()

/*
 * Sends the current STAGE over the CANBUS
 */
void sendCANstage(int stage){
  //Build the CANBUS message
  CAN_TX_msg.id = (ALTIMETER_MOD_CANID+FLIGHT_STAGE_CANID);
  CAN_TX_msg.len = 1;
  
  CAN_TX_msg.buf[0] = (stage)&0xFF;
  
  canb.write(CAN_TX_msg);     //send
}//sendCANstage()

/*
 * Sends the current temperature over CANBUS
 */
void sendCANtemp(float temp){
  //pushes decimals to first 8 bits
  uint32_t tempint = (temp*100);
  
  //Start shifting bits (b0 = LSB)
  uint8_t b0 = tempint & 0xFF;
  uint8_t b1 = tempint>>8 & 0xFF;
  uint8_t b2 = tempint>>16 & 0xFF;
  uint8_t b3 = tempint>>24 & 0xFF;
  
  //Build the CANBUS message
  CAN_TX_msg.id = (ALTIMETER_MOD_CANID+TEMP_CANID);
  CAN_TX_msg.len = 4;
  
  CAN_TX_msg.buf[0] = b0;
  CAN_TX_msg.buf[1] = b1;
  CAN_TX_msg.buf[2] = b2;
  CAN_TX_msg.buf[3] = b3;
  
  canb.write(CAN_TX_msg);     //send
}//sendCANtemp()

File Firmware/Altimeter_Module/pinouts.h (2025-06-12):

// Header file that contains all pinouts for this module
#define BATT_SENSE_PIN PB0
#define CURR_SENSE_PIN PB1
#define BOOT1_PIN PB2
#define RGB_DATA_PIN PB3
#define ACCEL_INT1_PIN PB5
#define ACCEL_INT2_PIN PB6
#define GYRO_INT_PIN PB7
#define CAN_RX_PIN PB8
#define CAN_TX_PIN PB9
#define SCL_PIN PB10
#define SDA_PIN PB11
#define FLASH_CS_PIN PB12
#define FLASH_SCK_PIN PB13
#define FLASH_MISO_PIN PB14
#define FLASH_MOSI_PIN PB15

#define FIRE_DROGUE_PIN PA1
#define CONT_DROGUE_PIN PA2
#define FIRE_MAIN_PIN PA3
#define CONT_MAIN_PIN PA4
#define BUZZER_B_PIN PA7
#define BUZZER_A_PIN PA8
#define USB_TX_PIN PA9
#define USB_RX_PIN PA10
#define FLASH_RESET_PIN PA11
#define SW_DIO_PIN PA13
#define SW_CLK_PIN PA14
#define STATUS_LED_PIN PA15

#define MS5611_ADDR 0x76
#define MPU6050_ADDR 0x69
#define KX134_ADDR 0x1F

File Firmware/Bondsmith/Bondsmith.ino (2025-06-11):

/*
 * Authors: Kennan Bays
 * Created: Jun.3.2025
 * Updated: Jun.10.2025
 * Hardware: Bondsmith PCB Rev1.0 (STM32F103C8T6)
 * Environment: Arduino 1.8.10, STM32duino 2.7? (likely works with newer cores)
 * Purpose: Firmware for the Bondsmith Motherboard inside the QRET 2025 briefcase ground station.
 *    Firmware facilitates measuring rail voltages, battery voltages, current consumption, fan RPM,
 *    button states, lid open/close state, and PSU temperature, reporting them over Serial. Also can
 *    be send commands to change which battery is being used, change fan speed, toggle 12V peripheral
 *    pins (VRX, Aux, RGB) and change the colours of the RGB indicator LEDs.
 *
 * Upload Settings:
 * - Board Part Number: STM32F103C8Tx [!!!]
 * - USART Support: Enabled (Generic serial)
 * - USB Support: None
 * - Optimize: Smallest
 * - Upload Method: STM32CubeProgrammer
 * 
 * KNOWN HARDWARE PROBLEMS:
 * - The resistor dividers for the 5V and 12V rail monitoring need a bypass capacitor as the divider is too high impedance. Workaround was longer ADC sampling time.
 * - The "BATT1_EN" and "BATT2_EN" signals exposed for LED indicators is inverted (HIGH disables a battery), thus the LEDs are inverted. Swap the GND pin to 3.3V to fix.
  */


#include "pinouts.h"
#include <HardwareSerial.h>
#include <movingAvg.h>          // https://github.com/JChristensen/movingAvg
#include <Adafruit_NeoPixel.h>
//TODO: Include STM32duino low power library to improve power consumption



// # # # # DEFINITIONS # # # # 
//#define FW_SIGNATURE "Jun.5.2025" // Firmware signature string. Update after major changes; allows end-user to check firmware version.
#define SERIAL_BAUD_RATE 115200
#define NUM_RGB_LEDS 5

// # # # # CONSTANTS # # # #
// Internal STM32 V(ref) voltage (default 1200mV)
const uint16_t STM_INT_REF = 1206; //CAL'D (experimental)
// Voltage/Current sense resistor divider ratios (experimentally measure for better accuracy)
const float BATT1_SENSE_DIV = 8.5812; //CAL'D (15.12, 1.762)
const float BATT2_SENSE_DIV = 8.5231;  //CAL'D (15.12, 1.774)
const float RAIL5_SENSE_DIV = 1.9996; //CAL'D (5.091, 2.546)
const float RAIL12_SENSE_DIV = 4.6286;  //CAL'D (12.09, 2.612)
// Temperature sensor divider resistor (measure for better accuracy)
const uint32_t TEMP_SENSE_R1_OHMS = 10030; //CAL'D
const uint16_t SENSOR_MEASURE_INT = 50; // period (ms) for sensor measurements
const uint16_t REPORT_INTERVAL = 1000; // period (ms) for printing reports to rasppi
// Cooling fan management curve
const uint8_t FAN_HYSTERESIS = 3; //Hysteresis (deg C) for when to turn the fan down again after hitting a threshold
const uint8_t FAN_OFF_TO_LOW = 35;  // Deg C when the fan will kick on to low speed
const uint8_t FAN_LOW_TO_HIGH = 45; // Deg C when the fan will kick on to high speed
const uint8_t FAN_HIGH_TO_LOW = FAN_LOW_TO_HIGH-FAN_HYSTERESIS;
const uint8_t FAN_LOW_TO_OFF = FAN_OFF_TO_LOW-FAN_HYSTERESIS;
const uint8_t FAN_LOW_POWER = 190;  // Low fan power
const uint8_t FAN_HIGH_POWER = 255; // High fan power


// # # # # GLOBAL VARIABLES # # # #
uint32_t lastMeasureMillis = 0; // last millis() when measurements were taken
uint32_t lastReportMillis = 0; // last millis() when a pi report was made

uint8_t curFanPower = 0; // Current fan power (0-255)
volatile uint32_t fanTachPulses = 0; // Increments as fan tachometer pulses

// Most recent filtered sensor measurements
uint16_t lastRail3v3Volt = 0; //mV
uint16_t lastRail5Volt = 0; //mV
uint16_t lastRail12Volt = 0; //mV
uint32_t lastBatt1Volt = 0; //mV
uint32_t lastBatt2Volt = 0; //mV
uint16_t lastCurrent = 0; //mA
float lastPsuTemp = 0; //deg C
bool lastB1Down = false;
bool lastB2Down = false;
bool lastB3Down = false;
bool lastLidClosed = false;
uint16_t lastFanRPM = 0;


// # # # # GLOBAL OBJECTS # # # #
HardwareSerial pi(PI_RX_PIN, PI_TX_PIN);

movingAvg rail3v3RawFilter(20);
movingAvg rail5RawFilter(20);
movingAvg rail12RawFilter(20);
movingAvg batt1RawFilter(20);
movingAvg batt2RawFilter(20);
movingAvg currentRawFilter(20);

Adafruit_NeoPixel indicators(NUM_RGB_LEDS, RGB_DATA_PIN, NEO_GRB + NEO_KHZ800);

/*
 * Reads internal voltage reference and back-calculates
 * the system Vdd (VDDA) using a calibrated Vref consant.
 * Returns the average across several samples (MAX ~32k
 * samples supported). Probably works with many STM32F1xx
 * chips.
 * 
 * Inspired by the STM32duino Internal_channels example
 */
uint16_t measureVref(uint16_t samples) {
  // Take samples
  uint16_t result;
  uint32_t accum = 0;
  for (int i = 0; i < samples; i++) {
    result = analogRead(AVREF);
    accum += ((STM_INT_REF * 4096L) / result); // Back-calculate VDDA in mV
  }//for
  return accum/samples; //Average
}//measureVref(int)


// Called when fan tach pin pulses
void onFanTach() {
  fanTachPulses++;
}//onFanTach()


void setup() {
  // Configure pinmodes
  pinMode(BATT1_SENSE_PIN, INPUT);
  pinMode(BATT2_SENSE_PIN, INPUT);
  pinMode(CURR_SENSE_PIN, INPUT);
  pinMode(RAIL_5V_SENSE_PIN, INPUT);
  pinMode(PSU_TEMP_PIN, INPUT);
  pinMode(RAIL_12V_SENSE_PIN, INPUT);
  pinMode(CURR_SENSOR_PWR_PIN, OUTPUT);
  pinMode(BATT1_DISABLE_PIN, OUTPUT);
  pinMode(BATT2_DISABLE_PIN, OUTPUT);
  pinMode(FAN_PWM_PIN, OUTPUT);
  pinMode(FAN_TACH_PIN, INPUT);
  pinMode(STATUS_LED_PIN, OUTPUT);
  pinMode(RGB12_B_PIN, OUTPUT);
  pinMode(RGB12_G_PIN, OUTPUT);
  pinMode(RGB12_R_PIN, OUTPUT);
  pinMode(LID_SENSE_PIN, INPUT);
  pinMode(BUTT3_SENSE_PIN, INPUT);
  pinMode(BUTT2_SENSE_PIN, INPUT);
  pinMode(BUTT1_SENSE_PIN, INPUT);
  pinMode(AUX_PWR_ENABLE_PIN, OUTPUT);
  pinMode(RGB_DATA_PIN, OUTPUT);
  pinMode(VRX_PWR_ENABLE_PIN, OUTPUT);

  // Immediately switch to the higher-voltage battery (TODO: IMPLEMENT)
  digitalWrite(BATT1_DISABLE_PIN, LOW);
  digitalWrite(BATT2_DISABLE_PIN, LOW);

  // Config fan tach interrupt
  attachInterrupt(digitalPinToInterrupt(FAN_TACH_PIN), onFanTach, FALLING);

  // Turn on VRX and AUX ports
  digitalWrite(AUX_PWR_ENABLE_PIN, HIGH);
  digitalWrite(VRX_PWR_ENABLE_PIN, HIGH);

  // Turn fan on 100%
  setFanPower(255);

  // Turn on current sensor (TODO: Disable this for power saving in the future)
  digitalWrite(CURR_SENSOR_PWR_PIN, HIGH);

  // Initialize RGB indicator LEDs
  indicators.begin();
  
  // Flash debug LED to signal startupp
  for (uint8_t i=0; i<8; i++) {
    digitalWrite(STATUS_LED_PIN, HIGH);
    delay(100);
    digitalWrite(STATUS_LED_PIN, LOW);
    delay(100); 
  }//for

  // Start Serial comms
  pi.begin(SERIAL_BAUD_RATE);
  pi.println("Bondsmith starting...");

  // Configure ADC
  analogReadResolution(12); //12-bit

  // Initialize moving average filters
  rail3v3RawFilter.begin();
  rail5RawFilter.begin();
  rail12RawFilter.begin();
  batt1RawFilter.begin();
  batt2RawFilter.begin();
  currentRawFilter.begin();

}//setup()
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

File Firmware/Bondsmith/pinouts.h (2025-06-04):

// Header file that contains all pinouts for Bondsmith
#define BATT1_SENSE_PIN PA0
#define BATT2_SENSE_PIN PA1
#define CURR_SENSE_PIN PA2
#define RAIL_5V_SENSE_PIN PA3
#define PSU_TEMP_PIN PA4
#define RAIL_12V_SENSE_PIN PA5
#define CURR_SENSOR_PWR_PIN PA6
#define BATT1_DISABLE_PIN PA7
#define BATT2_DISABLE_PIN PA8
#define PI_TX_PIN PA9
#define PI_RX_PIN PA10
#define FAN_PWM_PIN PA11
#define FAN_TACH_PIN PA12
#define STATUS_LED_PIN PA15

#define GPIO_PB0_PIN PB0
#define GPIO_PB1_PIN PB1
#define RGB12_B_PIN PB3
#define RGB12_G_PIN PB4
#define RGB12_R_PIN PB5
#define LID_SENSE_PIN PB6
#define BUTT3_SENSE_PIN PB7
#define BUTT2_SENSE_PIN PB8
#define BUTT1_SENSE_PIN PB9
#define GPIO_SCL_PIN PB10
#define GPIO_SDA_PIN PB11
#define AUX_PWR_ENABLE_PIN PB13
#define RGB_DATA_PIN PB14
#define VRX_PWR_ENABLE_PIN PB15

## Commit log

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2023-11-23 Created power module KiCAD project
    Previously called the "connections" module - "power" module seems more fitting for its purpose. Also to avoid confusion between it and the backplane PCB.
    [Power_Module.kicad_pcb, Power_Module.kicad_sch]
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2023-11-26 added GPS module from last year added labels to processor
    [GPS_Module.kicad_sch]
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2023-11-26 Updated branch name to reflect my work will be in here too, formatted communications schematic/layout pages, integrated already created subcircuit schematics into communications schematic, and added 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
    [Communications_Module.kicad_pcb, Communications_Module.kicad_sch]
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2024-01-23 added some datasheets and schematics and updates gps module
    [GPS_Module.kicad_sch]
2024-01-25 Sourced datasheets, symbols, and footprints for all parts on list. Added all relevant symbols to schematic for the most part.
    [Communications_Module.kicad_sch]
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2024-01-26 Added last few sub-circuits (buzzer, SWD), connected a bunch of pins between modules and STM, changed ideal diode circuit. Overall, rough draft minus edge connector
    [Communications_Module.kicad_sch]
2024-01-26 Forgot LEDs in last commit so adding them, need a bit more input for RGB tho
    [Communications_Module.kicad_sch]
2024-01-27 Progress 01/27 5PM
    - Added Accelerometer and Pressure sensor + pull up resistors for I2C
    - Included repeated (WIP) subcircuits from other modules eg. CANBUS, current sensing
    [Altimeter_Module.kicad_pcb, Altimeter_Module.kicad_sch]
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2024-01-31 Added correct RGB symbol, added/clarified some notes & questions on schematic.
    [Communications_Module.kicad_sch]
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2024-02-02 Added to do list, secured edge connector pins, GPS Backup offically on the Daughter
    [GPS_Module.kicad_sch]
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2024-02-04 completed buzzer and finalized LEDs and GPS Backup power source
    [GPS_Module.kicad_sch]
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2024-02-28 All part numbers added + parallel caps and resistors removed
    All part numbers added + parallel caps and resistors removed
    [Power_Module.kicad_sch]
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2024-02-28 Fixed stack edge connector connections
    Fixed stack edge connector connections
    [Power_Module.kicad_sch]
2024-02-29 Needs Review but mostly done apart from a few pins on the MCU
    [Sensors_Module.kicad_sch]
2024-02-29 Various Small Updates
    - Switched US resistor symbols to standard ones
    - Added more RGB LEDs
    - Added battery measurement circuit
    - Connected edge connector properly
    - Rearranged various components
    [Communications_Module.kicad_sch]
2024-02-29 Added STM32 Reset+Bootmode buttons
    [Communications_Module.kicad_sch]
2024-02-29 update 5:07 2/29
    buzzer
    [Altimeter_Module.kicad_sch]
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2024-03-02 Various Revisions
    -Added footprints and 3D models
    -Also adjusted RFM95 pinouts
    -Added more LCSC part numbers
    [10118194-0001LF-USB.step, Communications_Module.kicad_sch, ISO1042BDWVR.step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]
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2024-03-03 Various LED Tweaks
    - Changed from 4 to 2 RGB LEDs
    - Added dedicated debug LED (YLW)
    - Updated resistor for power LED (GRN)
    [Communications_Module.kicad_sch]
2024-03-03 Cleaned up schematic
    -Deleted images & rearranged items
    -Tied LM66100 "ST" pins to GND
    -Changed RF's DIO5 to DIO2
    [Communications_Module.kicad_sch]
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2024-03-07 Pulled several changes from communications module
    -Ensured parts all have footprints
    -Redesigned supercapacitor charging circuit
    -Set STM32 pinouts
    -Added more test points
    -Removed 2 RGB LEDs, added debug LED
    [10118194-0001LF-USB.step, GPS_Module.kicad_sch, ISO1042BDWVR.step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]
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2024-03-07 Added flash LCSC # and fixed stack connector pinout
    [Communications_Module.kicad_sch]
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2024-03-09 Fixed libraries and added updated edge connector
    [Power_Module.kicad_sch]
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2024-03-09 Fixed footprints & added proper power connectors
    [Power_Module.kicad_sch, c-2-1445057-2-d-3d.stp]
2024-03-09 Fixed capacitor footprints
    [Power_Module.kicad_sch]
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2024-03-10 Pull changes from Communications module
    -Added footprints & symbols
    -Added completed subcircuits (power MUX, debug LEDs, etc)
    -Added revised stack edge connector
    -Lightly organized schematic
    [Altimeter_Module.kicad_sch]
2024-03-10 Revert "starting PCB layout"
    This reverts commit 0f9aa6cd92282e41b038e1a8acfc0611b64ad155.
    [GPS_Module.kicad_pcb, GPS_Module.kicad_sch]
2024-03-10 Revert "moved daughter baord to seperate kicad project"
    This reverts commit fcbb505597515332a77ecb4c4305073f0cf4bc85.
    [GPS_Daughter_Board.kicad_pcb, GPS_Daughter_Board.kicad_sch]
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2024-03-11 Fixed pressure sensor & accelerometer
    [Altimeter_Module.kicad_sch]
2024-03-11 Replaced ADXL350 with MPU6050
    ADXL350 was never a verified part - it's actually an accelerometer, not a gyroscope (JLCPCB's listing is incorrect). Replaced it with the inexpensive MPU6050.
    [Altimeter_Module.kicad_sch]
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2024-03-11 Just a few tough traces left, no antenna yet. 'So close but so far'
    [Communications_Module.kicad_pcb, Communications_Module.kicad_sch]
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2024-03-13 Small adjustments
    -Changed ADC filter caps to 0805 MLC ones
    -Added some LCSC part numbers
    -Fixed unintentional voltage divider on buzzer circuit
    -Fixed some missing symbol library errors
    [Altimeter_Module.kicad_sch]
2024-03-13 Switched to using secondary channel power rails
    Was previously just using the primary rails. Altimeter should be using the secondary rails (for isolation + redundancy)
    [Altimeter_Module.kicad_sch]
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2024-03-13 Replaced bootmote & reset button footprints
    Changed from PTS636SK to a PTS1187A as the latter is a JLCPCB basic component (cost-saving)
    [Altimeter_Module.kicad_sch]
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2024-03-13 Fixed footprints and added PCB template
    [Altimeter_Module.kicad_pcb, Altimeter_Module.kicad_sch]
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2024-03-14 Fixed voltage divider on buzzer circuit
    [GPS_Module.kicad_sch]
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2024-03-14 Updated LMR51430 footprint
    Shrunk it slightly and changed any "Unspecified" pins to "Passive"
    [Power_Module.kicad_sch]
2024-03-14 Small tweaks
    -Added testpoints
    -Upgrade reverse polarity protection from AO4485 to to AO4447A
    -Selected LED colours & resistors
    [Power_Module.kicad_sch]
2024-03-14 Small hardware tweaks (PCB update required)
    -Changed bootmode/reset switches from PTS636 to TS1187
    -Fixed buzzer gate driver
    -Disconnected debug LED from edge connector
    -Updated capacitor footprints for analog filtering
    [Communications_Module.kicad_sch]
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2024-03-16 Various changes
    -Added many symbols and footprints
    -Pulled base changes from other schematics
    -Organized schematic
    -Added attribution text
    [Sensors_Module.kicad_pcb, Sensors_Module.kicad_sch]
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2024-03-17 All DRC passed, fixed silkscreen issues
    [Communications_Module.kicad_pcb, Communications_Module.kicad_sch]
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2024-03-19 Added Digikey + LCSC part numbers
    Also updated MS5607 footprint to be easier to hand-solder
    [Altimeter_Module.kicad_sch, MS560702BA03-50.step]
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2024-03-19 Reset PCB layout
    [Altimeter_Module.kicad_pcb]
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2024-03-20 Updated PCB "Copper to edge clearance" to 0.3mm
    PCB needs updating accordingly
    [Communications_Module.kicad_pcb]
2024-03-20 Tweaked arrangement and updated copper clearance
    -Set "copper to edge clearance" to 0.3mm
    -Moved molex connectors 8mm back from board edge
    -Decreased horizontal margin from 2.5mm to 1.25mm
    -Increased several traces from 1mm to 2mm
    -Added a few more copper pours
    [Power_Module.kicad_pcb]
2024-03-20 Updated layout to pass DRC with new copper-edge clearance
    [Communications_Module.kicad_pcb]
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2024-03-26 Verified part numbers & made ERC pass
    Also cleaned up unnecessary footprints & added bulk filtering capacitor to GPS antenna board
    [GPS_Antenna_Board.kicad_pcb, GPS_Antenna_Board.kicad_sch, GPS_Module.kicad_sch]
2024-03-26 PCB Adjustments + Add USB-C port (DRC pass)
    - Rerouted several traces to reduce via hopping
    - Routed CANBUS wires as differential pair
    - Rearranged some items
    - Swapped USB-MicroB port for USB-C port
    - Added silkscreen labels
    [GPS_Module.kicad_pcb, GPS_Module.kicad_sch]
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2024-03-27 Fixed my horrendous via stitching precision
    [Communications_Module.kicad_pcb]
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2024-03-27 Minor Adjustments
    - Adjusted LED resistor values
    - Cleaned up PCB project lightly
    [Buck_PSU.kicad_sch, Power_Module.kicad_pcb, Power_Module.kicad_sch]
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2024-05-29 Fixed SATA pinout + Dimmed power LED
    Most SATA cables short pins 1,4,7 together as GND. For Rev 1.0, this meant the PPS, RESET, and GND pins were all tied together, effectively bricking the GPS.
    This has been revised by disconnecting pins 4 & 7, discarding the PPS signal entirely and then sharing pin 3 for EITHER the reset signal or external interrupt signal. Updated board routing as needed.
    Also quickly tweaked the power LED resistor so the LED is dimmer. (1.8k to 3.3k)
    [GPS_Antenna_Board.kicad_pcb, GPS_Antenna_Board.kicad_sch]
2024-05-29 Fixed supercap charger RCB
    Previous use of LM66100 ideal diode didn't work as, when power was lost, the ideal diode would stop functioning properly and would still let power through. Have swapped to a simple 1N5819 Schottky diode.
    Also broke out the TX/RX pins of the GPS for easier external programming, if needed.
    [GPS_Antenna_Board.kicad_pcb, GPS_Antenna_Board.kicad_sch]
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2024-05-29 Major updates
    -Changed to USB C connector
    -Added CP2102 USB-UART bridge
    -Added RunCam control pins
    -Added new magnetometer (BM1422AGMV)
    -Added BME680 sensor
    -Changed PWR LED resistor to 3.3k
    [Sensors_Module.kicad_sch]
2024-05-29 Removed load cell ADC & old magnetometer
    Screenshot of circuit was left for reference
    [Sensors_Module.kicad_sch]
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2024-06-06 Fixed incorrect pinout for BM1422AGMV (Rev 1.0A)
    [Sensors_Module.kicad_pcb]
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2024-06-17 fixed basic read MPU6050
    [MPU6050_basic_read.ino]
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2024-06-30 Deployed altimeter code
    Note that the flash size used for the flash table is known to cause problems, and that negative gyroscope/accelerometer values are not recorded. This code needs some tweaks, BUT this is what flew at SPAC24.
    Excellent work done by Brent & Tristan
    [Register_mapping.xlsx]
2024-06-30 Deployed sensors code
    Note that the flash table size is known to cause problems, and the incorrect camera power pin is used. This code needs some work, BUT its what flew at SPAC24.
    [Sensors_Module.ino]
2024-08-17 Fixed camera pin & started using pinouts def file
    [Sensors_Module.ino]
2024-08-17 Fixed flash logging bugs
    [Altimeter_Module.ino]
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2024-08-17 Enabled debug mode for GPS and fixed errors
    [GPS_Module.ino, debugmode.ino]
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2024-08-18 Fixed data logging bug & cleaned up MDE
    [Sensors_Module.ino]
2024-08-18 Fixed GPS so old connection doesn't count as a fix
    [GPS_Module.ino]
2024-08-18 Fixed altimeter drogue deployment, added main deployment
    [Altimeter_Module.ino]
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2024-08-19 Updated Start Up Buzzer
    [Communications_Module.ino, GPS_Module.ino, Sensors_Module.ino]
2024-08-20 Fixed last small bugs before final flashing
    [Altimeter_Module.ino, Sensors_Module.ino]
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2024-11-25 Quick note about the CP2102's reset pin error
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2025-02-12 Added CP2102 USB bridge
    Also bumped version up to V2.0 now that significant hardware changes (e.g. pinout changes) have been made. This breaks firmware backwards compatibility, and thus warrants a major version bump.
    [Altimeter_Module.kicad_pcb, Altimeter_Module.kicad_sch]
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2025-02-12 Adjusted schematic documentation
    Noted that battery sense circuit will remain for redundancy, and that QMA6100P accelerometer was used in place of KX134
    [Altimeter_Module.kicad_sch]
2025-02-13 Added revised buzzer driver circuit
    Changed to buzzer PS1240P02BT (previous stock issues), plus switched to using 2-pin inverse PWM drive via a TPM8837C H-Bridge IC. Now Vpp should be ~14.8V.
    [Altimeter_Module.kicad_sch]
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2025-02-14 Swapped SWD connector to SMD version
    [8890445_SWD_PINS.stp, Altimeter_Module.kicad_sch]
2025-03-06 Changed some drop-in replacement parts
    Some components have since gone out of stock; adjusting that here.
    - Changed to new USB-C port (C5178541)
    - Replaced AO3406AL with AO3406A (C5155213, stock issues)
    [Altimeter_Module.kicad_sch]
2025-03-06 Adjusted PCB layout
    - Moved E-Match connectors forward 4mm
    - Added polarity silkscreen to E-Match connectors
    - Adjusted attribution silkscreen
    - Added testpoint silkscreen labels
    [Altimeter_Module.kicad_pcb, Altimeter_Module.kicad_sch]
2025-03-07 Final adjustments + improved QMA6100 clearance
    [Altimeter_Module.kicad_pcb]
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2025-03-09 COSMETIC: Added missing 3D models
    [Altimeter_Module.kicad_pcb]
2025-06-04 Initial draft of firmware
    Just reports battery/rail voltage/current/temperature/fan speed/button states over serial every 1 second. Also automatically manages fan speed based on temperature. Fan RPM calculation doesn't work properly due to PWM freq being >> than fan speed, and thus PWM turns it on/off multiple times during a tach pulse, thus artificially inflating the pulse count significantly.
    Still need to add code for the RaspPi to request data rather than just being bombarded with it, make events for debounced button presses, make an interface to change between batteries, and make an interface for setting RGB LED colours. Maybe an interface for turning the VRX/AUX outputs on and off too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
    [Bondsmith.ino, pinouts.h]
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2025-06-12 Fixed bug where flash would just erase on startup & COMPILED BINARY
    [Altimeter_Module.ino]
